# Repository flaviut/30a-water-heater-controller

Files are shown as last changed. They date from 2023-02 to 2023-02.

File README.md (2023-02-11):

# 30A Water Heater Controller

This board contains a design for a water heater controller that is good for up to 30A water heaters.

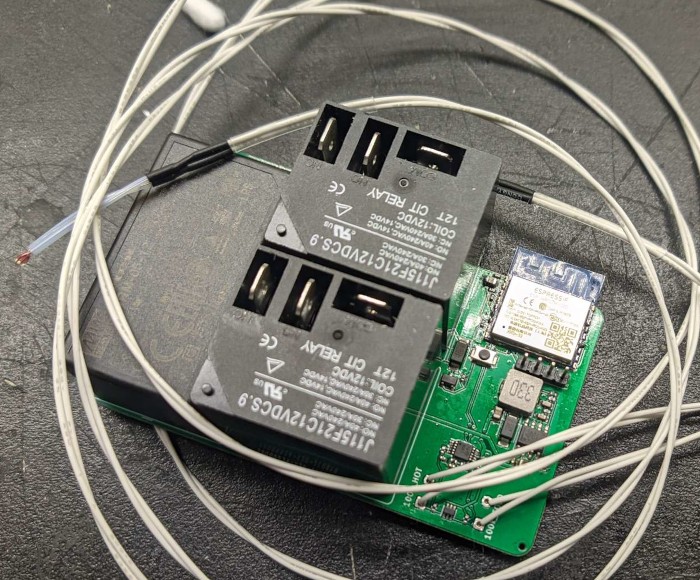
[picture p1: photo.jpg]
photo of assembled board


## Warranty

Working with high currents and mains voltages is dangerous. Death from electrical shock & house fires are both real risks with this project.

This project comes with no warranty, and is not examined by or listed by any NRTL. You are solely responsible for determining if it is safe.

## Manufacturing

The latest release contains all the files you need to have this PCB manufactured & 90% assembled by a vendor of your choice. I used JLCPCB.

The defaults are fine. You may wish to ask them to not assemble the thermistor connectors to save a couple bucks.

## Additional BOM

- 1x 100k NTC Temperature Sensor 3950 (2 are supported, but only 1 is useful)
- 1x IRM-05-12 power supply
- 2x J115F21C12VDCS.9
- 4x large wire nuts
- 4x 10AWG UL listed crimp connectors
- 1ft red/1ft black 10AWG coarse-stranded wire
- Suitable electronics enclosure

## Tools

- Soldering iron
- Crimping tool

## Assembly

- Flash ESPHome onto the ESP8266 using the included `esphome.yaml` as a template
- *Turn the circuit breaker off & use a non-contact voltage tester to ensure it is off*
- Cut wire into four 6in pieces; strip one end of each for a crimp connection & the other end for wire nut
- Crimp one end of each wire.
- Solder thermistor header, relays, and power supply. Optionally solder programming header.
- Connect black wires to one relay, red wires to the other
  - one wire to common
  - one wire to normally closed
- Place everything in the enclosure
- Use the wire nuts to connect the pigtails on the common terminals to the mains wiring
- Use the wire nuts to connect the pigtails on the normally closed terminals to the water heater
- Connect one temperature sensor to `100k_HOT`, and feed it out of the enclosure
  - this wire should not be near the mains wiring at any point
- Place one end of the temperature sensor wire down the hole that the top overpressure valve comes out of, and use some paper towels or tape to insulate it in

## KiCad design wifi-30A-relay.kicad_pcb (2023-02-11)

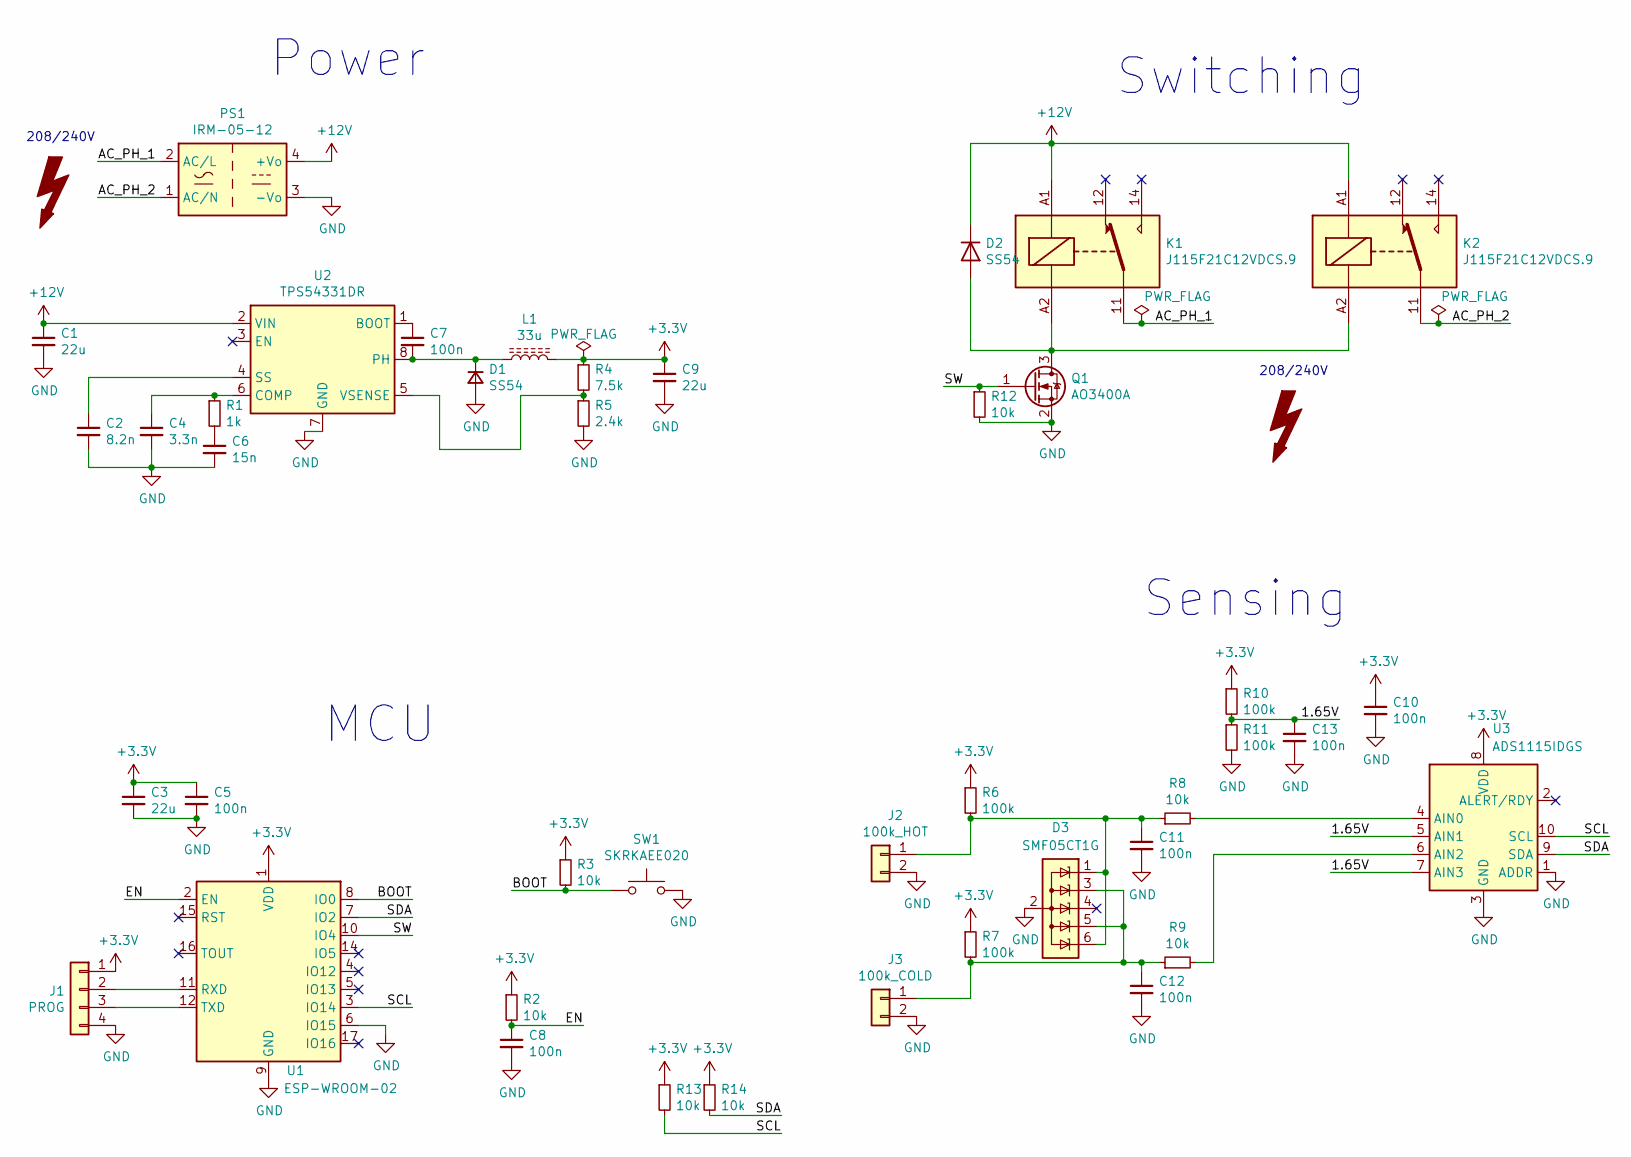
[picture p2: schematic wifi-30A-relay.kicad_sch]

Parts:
C1, C3, C9: 22u; C_0805_2012Metric; LCSC C45783
C2: 8.2n; C_0603_1608Metric; LCSC C27920
C4: 3.3n; C_0603_1608Metric; LCSC C1613
C5, C7, C8, C10, C11, C12, C13: 100n; C_0402_1005Metric; LCSC C1525
C6: 15n; C_0603_1608Metric; LCSC C1596
D1, D2: SS54; D_SMA; LCSC C22452
D3: SMF05CT1G; SOT-363_SC-70-6; LCSC C15879
J1: PROG; PinHeader_1x04_P2.54mm_Vertical
J2: 100k_HOT; JST_XH_B2B-XH-AM_1x02_P2.50mm_Vertical; LCSC C2979476
J3: 100k_COLD; JST_XH_B2B-XH-AM_1x02_P2.50mm_Vertical; LCSC C2979476
K1, K2: J115F21C12VDCS.9; Relay_SPDT_CIT-J115F2
L1: 33u; L_TDK_SLF6028; LCSC C149577
PS1: IRM-05-12; Converter_ACDC_MeanWell_IRM-05-xx_THT
Q1: AO3400A; SOT-23; LCSC C20917
R1: 1k; R_0402_1005Metric; LCSC C11702
R2, R3, R8, R9, R12, R13, R14: 10k; R_0402_1005Metric; LCSC C25744
R4: 7.5k; R_0402_1005Metric; LCSC C25918
R5: 2.4k; R_0402_1005Metric; LCSC C25882
R6, R7, R10, R11: 100k; R_0402_1005Metric; LCSC C25741
SW1: SKRKAEE020; SW_Push_SPST_NO_Alps_SKRK; LCSC C115357
U1: ESP-WROOM-02; LCSC C529584
U2: TPS54331DR; SOIC-8_3.9x4.9mm_P1.27mm; LCSC C9865
U3: ADS1115IDGS; TSSOP-10_3x3mm_P0.5mm; LCSC C37593

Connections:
+3.3V: C3.1, C5.1, C9.1, C10.1, J1.1, L1.2, R2.1, R3.1, R4.1, R6.1, R7.1, R10.1, R13.1, R14.1, U1.1 (VDD), U3.8 (VDD)
+12V: C1.1, D2.1 (K), K1.A1, K2.A1, PS1.4 (+Vo), U2.2 (VIN)
/1.65V: C13.1, R10.2, R11.1, U3.5 (AIN1), U3.7 (AIN3)
/AC_PH_1: K1.11, PS1.2 (AC/L)
/AC_PH_2: K2.11, PS1.1 (AC/N)
/BOOT: R3.2, SW1.1, U1.8 (IO0)
/EN: C8.1, R2.2, U1.2 (EN)
/SCL: R13.2, U1.3 (IO14), U3.10 (SCL)
/SDA: R14.2, U1.7 (IO2), U3.9 (SDA)
/SW: Q1.1 (G), R12.1, U1.10 (IO4)
GND: C1.2, C2.2, C3.2, C4.2, C5.2, C6.2, C8.2, C9.2, C10.2, C11.2, C12.2, C13.2, D1.2 (A), D3.2 (A), J1.4, J2.2, J3.2, PS1.3 (-Vo), Q1.2 (S), R5.2, R11.2, R12.2, SW1.2, U1.6 (IO15), U1.9 (GND), U1.13 (GND), U1.18 (GND), U1.19 (GND), U2.7 (GND), U2.9 (GND), U3.1 (ADDR), U3.3 (GND); also elsewhere on the board
unnamed: C2.1, U2.4 (SS)
unnamed: C4.1, R1.1, U2.6 (COMP)
unnamed: C6.1, R1.2
unnamed: C7.1, U2.1 (BOOT)
unnamed: C7.2, D1.1 (K), L1.1, U2.8 (PH)
unnamed 16: C11.1, D3.1 (K), D3.6 (K), J2.1, R6.2, R8.1; also elsewhere on the board
unnamed 17: C12.1, D3.3 (K), D3.5 (K), J3.1, R7.2, R9.1; also elsewhere on the board
unnamed: D2.2 (A), K1.A2, K2.A2, Q1.3 (D)
unnamed: J1.2, U1.11 (RXD)
unnamed: J1.3, U1.12 (TXD)
unnamed: R4.2, R5.1, U2.5 (VSENSE)
unnamed: R8.2, U3.4 (AIN0)
unnamed: R9.2, U3.6 (AIN2)

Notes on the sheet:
Power
MCU
Switching
208/240V
Sensing

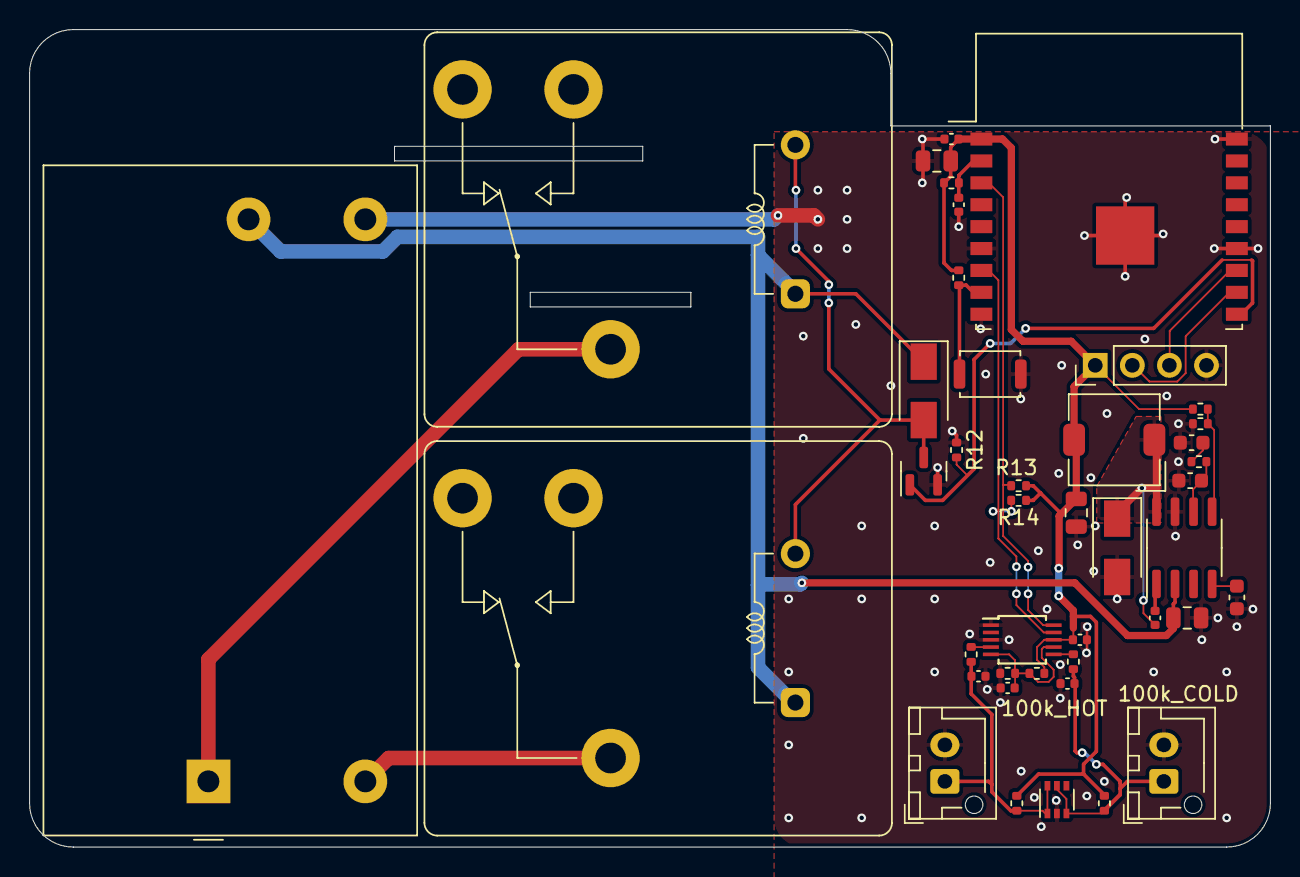
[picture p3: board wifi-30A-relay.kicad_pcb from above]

Board: 2 copper layers, 85.0 x 56.0 mm, 42 parts (0 on the bottom side), 24 nets.

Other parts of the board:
100k_COLD: 100k_COLD; JST_XH_B2B-XH-AM_1x02_P2.50mm_Vertical
100k_HOT: 100k_HOT; JST_XH_B2B-XH-AM_1x02_P2.50mm_Vertical

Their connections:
GND: 100k_COLD.2, 100k_HOT.2; also elsewhere on the board
unnamed 16: 100k_HOT.1; also elsewhere on the board
unnamed 17: 100k_COLD.1; also elsewhere on the board

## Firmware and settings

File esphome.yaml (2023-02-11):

substitutions:
  # https://esphome.io/guides/configuration-types.html#substitutions
  device_name: waterheater # hostname & entity_id
  friendly_name: Water Heater # Displayed in HA frontend

esphome:
  # https://esphome.io/components/esphome
  name: ${device_name}
  platform: ESP8266
  board: esp_wroom_02

logger:
  baud_rate: 0


# Enable Home Assistant API
api: {password: !secret api_password}
# enable ota updates
ota: {password: !secret api_password}

wifi:
  ssid: !secret wifi_ssid
  password: !secret wifi_password

output:
  - platform: gpio
    pin: GPIO4
    id: heater_gpio

switch:
  - platform: output
    # https://esphome.io/components/switch/output.html
    id: heater
    output: heater_gpio

i2c:
  sda: 2
  scl: 14
  scan: true

ads1115:
  - address: 0x48

sensor:
  - platform: ads1115
    multiplexer: 'A0_GND'
    gain: 2.048
    update_interval: 312ms
    id: adc_top_in
    filters: [ { sliding_window_moving_average: { window_size: 32, send_every: 32, } } ]
  - platform: resistance
    id: res_top_in
    sensor: adc_top_in
    configuration: DOWNSTREAM
    resistor: 100kOhm
  - platform: ntc
    id: temp_top
    sensor: res_top_in
    name: ${friendly_name} Top Temperature
    calibration:
      b_constant: 3950
      reference_temperature: 25°C
      reference_resistance: 100kOhm

  - platform: ads1115
    multiplexer: 'A2_GND'
    gain: 2.048
    update_interval: 312ms
    id: adc_bot_in
    filters: [ { sliding_window_moving_average: { window_size: 32, send_every: 32, } } ]
  - platform: resistance
    id: res_bot_in
    sensor: adc_bot_in
    configuration: DOWNSTREAM
    resistor: 100kOhm
  - platform: ntc
    id: temp_bot
    sensor: res_bot_in
    name: ${friendly_name} Bottom Temperature
    calibration:
      b_constant: 3950
      reference_temperature: 25°C
      reference_resistance: 100kOhm

climate:
  - platform: thermostat
    id: hot_water_thermostat
    name: "Hot water heater"
    sensor: temp_top
    default_target_temperature_low: 60 °C
    min_heating_off_time: 0s
    min_heating_run_time: 300s
    min_idle_time: 0s
    default_mode: HEAT
    visual:
      max_temperature: 150 °F
      min_temperature: 120 °F
    heat_action:
      - switch.turn_off: heater
    idle_action:
      - switch.turn_on: heater
    # disable turning off the heat
    off_mode:
      - climate.control:
          id: hot_water_thermostat
          mode: HEAT

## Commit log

2021-08-16 Send off to production
    [file61184563.sch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]
2021-12-31 Fix programming error
    [wifi-50A-relay.kicad_pcb, wifi-50A-relay.kicad_sch]
2022-01-01 Clean up & add clearance DRC
    [wifi-50A-relay.kicad_pcb, wifi-50A-relay.kicad_sch]
2022-01-01 Add i2c pull-ups
    Forgotten in previous revisions
    [wifi-50A-relay.kicad_pcb, wifi-50A-relay.kicad_sch]
2022-01-02 Add more clearance
    This is unnessecary, but double the clearance between the mains &
    low-voltage side to 8mm since we have the room for it.
    [wifi-50A-relay.kicad_pcb]
2023-02-11 Some updates
    Uncommited, been around for a while
    [wifi-50A-relay.kicad_pcb]
2023-02-11 Migrate to new kicad
    [file61184563.sch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]
2023-02-11 Add kibot & fix DRC issues from kicad update
    [wifi-50A-relay.kicad_pcb]
2023-02-11 Fix erc issues
    [wifi-50A-relay.kicad_pcb, wifi-50A-relay.kicad_sch]
2023-02-11 Replace hand-soldered connectors with JST-XH
    These seem to be the most common connector for the 3950 100k NTC
    connectors found in 3d printers.
    [wifi-50A-relay.kicad_pcb, wifi-50A-relay.kicad_sch]
2023-02-11 Add readme & license, rename files
    [wifi-30A-relay.kicad_pcb, wifi-30A-relay.kicad_sch]
